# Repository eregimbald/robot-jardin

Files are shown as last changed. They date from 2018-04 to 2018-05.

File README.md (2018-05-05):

# robot-jardin

A controller to automate watering of an indoor tomato farm.

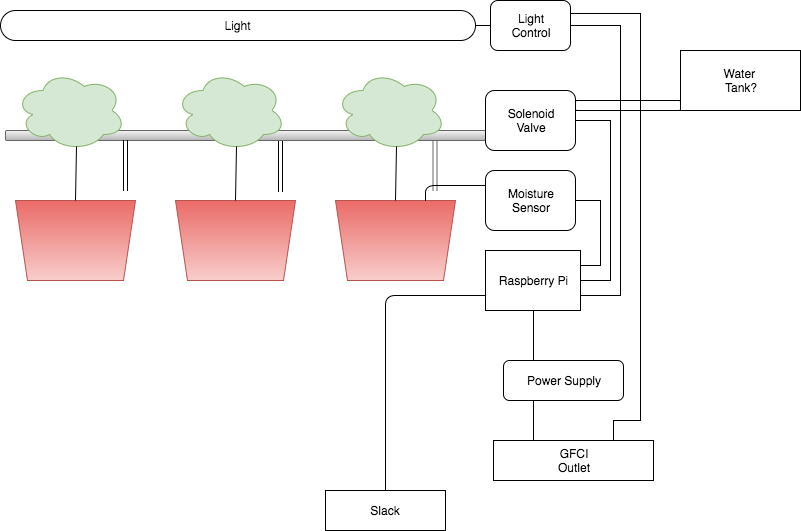
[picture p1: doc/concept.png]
Concept


* Moisture sensors for soil.
* Solenoids to control watering.
* Hoses and T pieces to direct water into the pots.
* A LED light system. Mechanism to turn on and turn off the lights.
* Slack integration to the Raspberry Pi for control and monitoring.

## Requirements

### Platforms

- Raspbian

#### Configuration

##### wifi-interface
```
sudo nano /etc/network/interfaces

auto wlan0
iface wlan0 inet static
  address 192.168.1.180
  netmast 255.255.255.0
  gateway 192.168.1.1
  wpa-conf /etc/wpa_supplicant/wpa_supplicant.conf
```

##### wpa_supplicant
```
sudo nano /etc/wpa_supplicant/wpa_supplicant.conf

country=CA
ctrl_interface=DIR=/var/run/wpa_supplicant GROUP=netdev
update_config=1

network={
    ssid="ssid"
    psk="psk"
}
```

##### Enabling services
```
sudo raspi-config
Interfacing options
Enable ssh
Enable SPI
```
## Packages

Everything runs on Python3

### spidev
```
sudo apt-get install python3-spidev
wget https://github.com/Gadgetoid/py-spidev/archive/master.zip
unzip master.zip
rm master.zip
cd py-spidev-master
sudo python setup.py install
cd ..
```
### Adafruit Python GPIO
```
sudo apt-get update
sudo apt-get install build-essential python-pip python-dev python-smbus git
git clone https://github.com/adafruit/Adafruit_Python_GPIO.git
cd Adafruit_Python_GPIO
sudo python setup.py install
sudo python3 -m pip install git+git://github.com/chrisb2/pi_ina219.git
```
### Adafruit Python MCP3008
```
sudo apt-get update
sudo apt-get install build-essential python-dev python-smbus python-pip
sudo pip3 install adafruit-mcp3008
```
## MISC
https://github.com/stefanwichmann/kelvin

https://www.amazon.ca/Irrigation-System-Sprinkler-Watering-Outdoor/dp/B073NBHRRD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

http://www.davidhunt.ie/water-droplet-photography-with-raspberry-pi/

## Hardware
* To use a piece of proto board, with a Raspberry PI expansion connector.
* Thru-hole components
* A power adapter rated at 12V, 5A (this is more than enough, but commodity available on Amazon).
* A 5V regulator circuit (So we can use the same power brick for powering the PI as well).
* moisture sensors connected to an AD converter.
* water valve solenoid controlled by transistors.
* lights controlled by switching a plug.

Where possible datasheets for the parts we have thought about using are in the doc/datasheets folder.

## Raspberry Pi
We have the Raspberry Pi 3B. We want to use this, for the familiarity of programming language (Python).

Also we wish to have slack integration for remote query, monitoring, and control of the device.

### Power adapter
We needed 12V to drive the solenoid.  The solenoid takes about 100mA of power.  Plus we need to consider the power requirements of the Raspberry Pi.

We found this on Amazon for $12
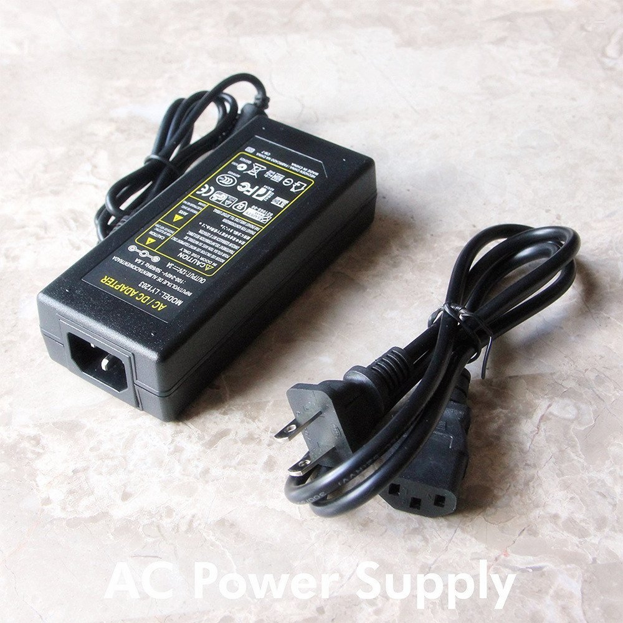
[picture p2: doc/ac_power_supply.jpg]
AC power supply


It sais it is for LED strip lighting. 12V rated at 5A.  This will be more than enough for our uses.

## Voltage Regulator
Rather than needing a 2nd power brick adapter for powering the Raspberry Pi, which is another plug in the power bar, and another cable, and that micro USB power connector that never stays plugged in nicely (compared to a barrel jack power connector), it would be better if we could power the Raspberry Pi from our power adapter.

Several sites recommend that you use the USB input, because the Pi has built in power protection for you, so that if you accidentally give it more than 5V input you won't wreck you Pi.

Here, if we use a good 5V stable voltage regulator, then we should not have any problems with our Pi. Unless we drop the Pi into a bucket of water. But really that will have more problems than electrical power input considerations.

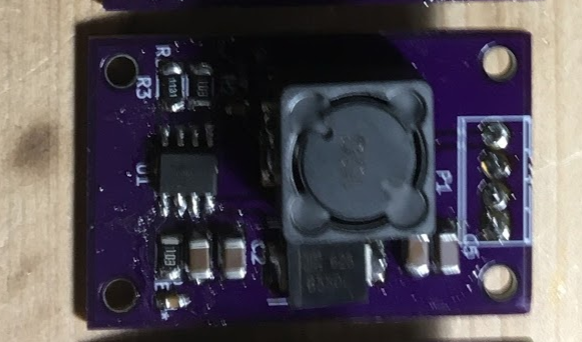
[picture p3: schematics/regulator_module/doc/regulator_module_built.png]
voltage regulator


This was from a different project where I was going to use this to drive some stepper motors. It should have enough power to handle the Pi.

### Moisture Sensor Inputs
These moisture sensors came with a small intermediate circuit board. This module has a comparator on it, so that it can produce a digial output. Our initial experiments found this to be not very reliable or accurate, or consistent. Turning that little potentiometer is hard to get it to where we want. And also, what does it mean. It does not leave room for adjustments in software. The board also has an analog output. But really this is just using a resistor to create a voltage divider type of circuit across the probe input. We have chosen to use this analog mode of the sensor.  So instead of needing to use this little circuit board it would be better if we just built the components onto our own circuit board. This way we can have just a pair of wires from the circuit board to the moisture sensor.

We analyzed the circuit board and it contains these components.

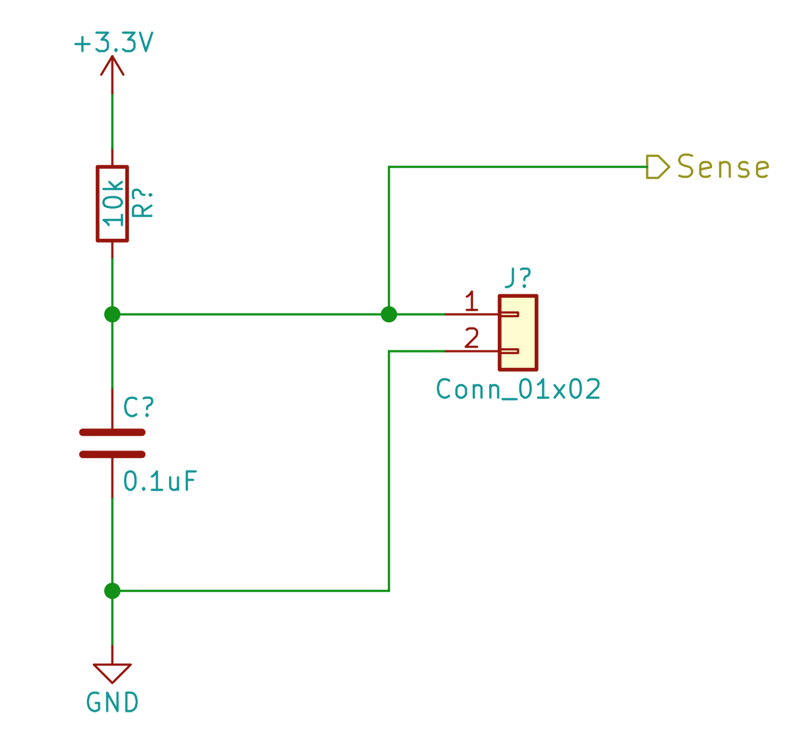
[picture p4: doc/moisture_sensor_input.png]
Moisture Sensor Input


Where the connector can be one of those screw terminal PCB mount connectors.  The wires we can use to go to the probe can be one of the pairs from a regular cat5 network cable type twisted pair wire, and then as long as we need to reach the potted plants from where the sensor is installed.

The sense goes straight into our analog to digital converter (currently the MCP3008 device).

When the soil is dry, the output will be a higher voltage. As the soil gets more moist, the probes will have a lower resistance, and thus create a lower voltage to the ADC.

Here we have chosen to use 3.3V as analog the input to the probes, since this is what the IO pins to the Raspberry Pi will use. The MCP3008 Supports separate Analog reference, but only as long as this is less than or equal to the VDD input.  Using 5V might possibly give us a better details when considering the small resistance that will be added from length of the wires to the probes. And 5V also lets us use faster samples. But really we are only going to be reading a few times a minute (or otherwise very low sample rate here).

#### One thing to note: Minimun dryness Threshold in software.

We should calibrate our software to expect the soil has a minimum dryness.  In that if the soil is below this threshold value then we do not attempt to try to water the soil. (e.g. we have a reading less than the maximum voltage possible).

This is because we have no way to differentiate between really dry soil, and if the probes are entirely not connected at all. such as there is no wires hooked up to the Raspberry Pi.  or in a more likely real world use case, if the wires on the probe corroded or the probe corroded or is no longer working.

In this situation (probes disconnected), when the soil appears dry to us, if we turn on the solenoid to let water in, the soil will never actually give a reading of "not dry" (because the probes are broken or disconnected). And we end up flooding the plants, and possibly making a mess of the apartment.

The proposal here then is to require the soil be some what moist. (e.g. so we are able to read a slightly lower voltage than just the max voltage). And then work with adjusting the soil moisture to be more moist within this. Assuming of course that we are able to read a minimum moisture that is within the range of what we would want the plants to be.

### Analog to digital controller
As discussed earlier, it is preferred we read the moisture sensor analog output, instead of its digital output, as our testing found there is not a very meaningful output from the moisture sensor digital output. Other than it is amusing for a test circuit on a breadboard.

The Raspberry Pi has no analog inputs. So we need something that can provide us with analog to digital conversion. For this we have selected the MCP3008 device.
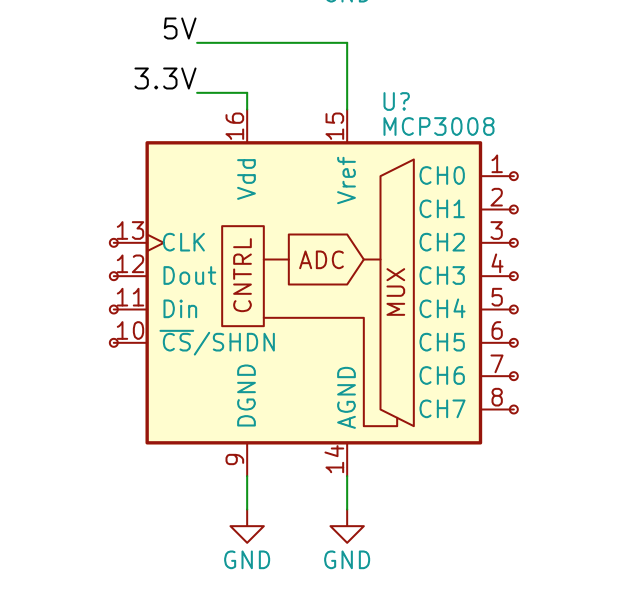
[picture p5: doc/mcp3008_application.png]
MCP3008 application


This is because this is a popular and inexpensive device, that is available in a 16-dip package, and has a good community supported driver.

It also has 8 channels. So we can readily connect up to 8 analog inputs. Such as moisture sensors, or anything that can provide us a voltage , like ambient light sensors, noise sensors, pressure sensors, potentiometers, etc.

Our immediate use will be a few moisture sensors.

### Solenoid Driver
We can use a basic digital IO pin from the Raspberry Pi to drive a solenoid.  The solenoid we have choosen works around 12V and uses about 100mA of current. A simple transistor driver circuit is good enough for this.

But we thought there should be some short circuit protection, in case we short out the wires to the solenoid, or the solenoid becomes connected to ground. This circuit below attempts to provide this protection.

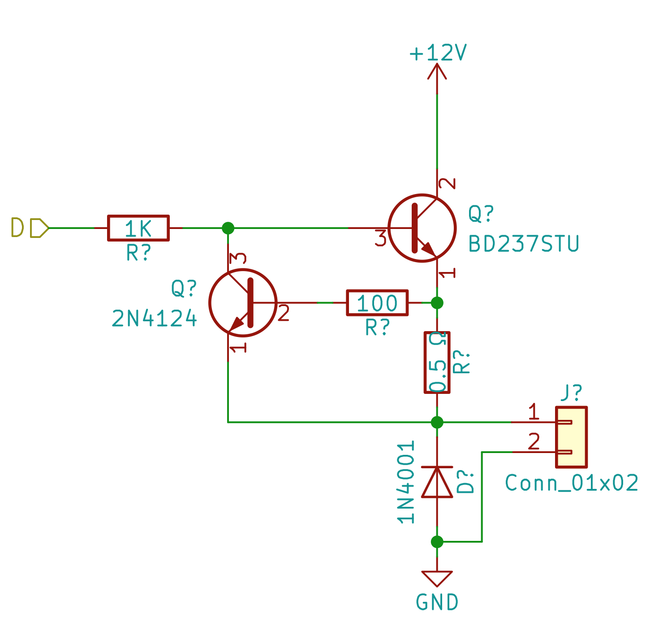
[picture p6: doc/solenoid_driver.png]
solenoid driver


The input from the Raspberry Pi digital IO pin of logic level HIGH will turn on the solenoid.  I prefer this option from the usual Ali express type of relay board. Where they have the opto isolators and relays, which can be used for anything from 12 VDC to 120 VAC. But they are active low inputs. Which means when you power on the Pi and the GPIO pins are logic level LOW by default, this will turn on the relays until our software boots up and asserts logic level HIGH to the pin.

Practically these relay boards do this to allow for more general compatibility with microcontrollers. Most semiconductor devices are able to sink more current (pull a pin low) then they are able to source current (pull a pin high). Here this is a mute point since we are using a transitor driver which uses much less current than the opto isolators (about 20 mA) on a relay board.

The 12V power for the solenoid will be provided by the power supply brick above.

### Plug Driver
To control the lighting for the plants we assume something that can handle being powered on and off by unplugging it. Such as a lamp with a switch that can be turned on and have the lamp come on when it is plugged in.

We have thought about using relays, but really it is more elegant to use Triac device with an opto isolator. This is the same feature and behavior as a solid state relay, only not as expensive. Here we are assuming we ae not using heavily inductive loads and thus do not require power conditioning or snubbering (beyond what the Trac provides).

Using these STMicroelectronics Snubberless series Triacs.
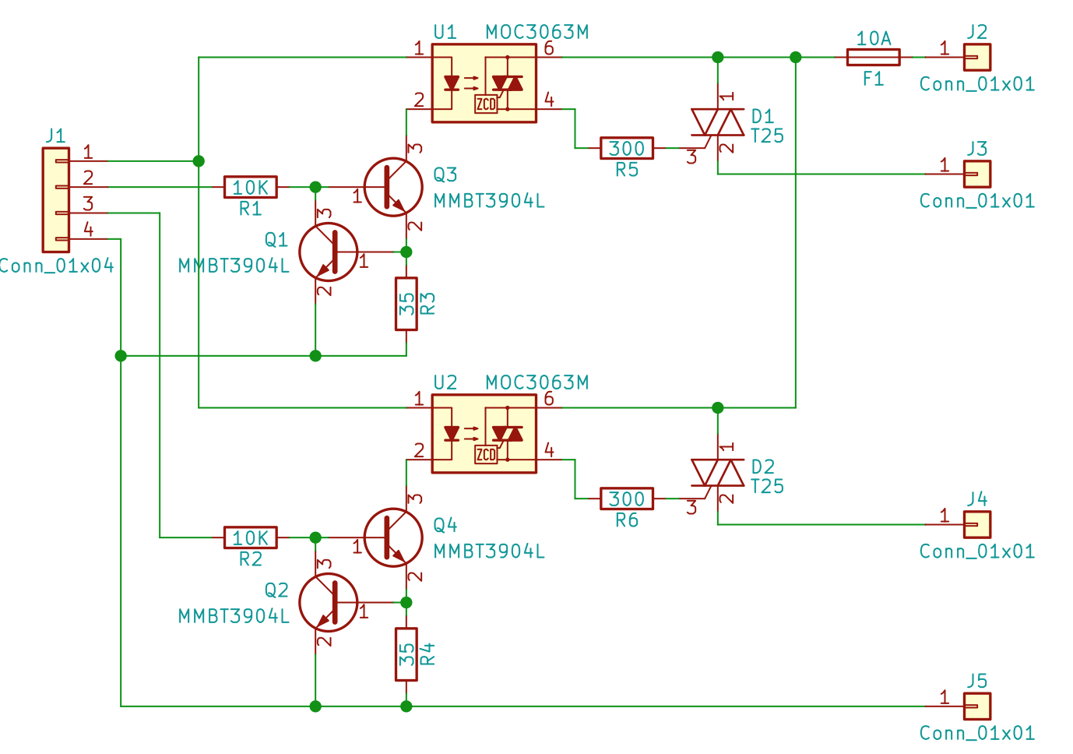
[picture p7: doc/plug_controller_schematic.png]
plug controller schematic


We have a connector there for AC ground to be also our ground.

This is actually two swiches. The idea being that in a standard duplex plug there are two halves (top and bottom). So that we can provide individual switching to each half. Which will allow us to plug two lights into a single duplex plug.

The board can be laid out small enough to fit inside a metal duplex outlet style box. So that we can provide control wires into the box.
I was invisioning an extension cord with the metal plug box on the end with this controller board inside the metal box.

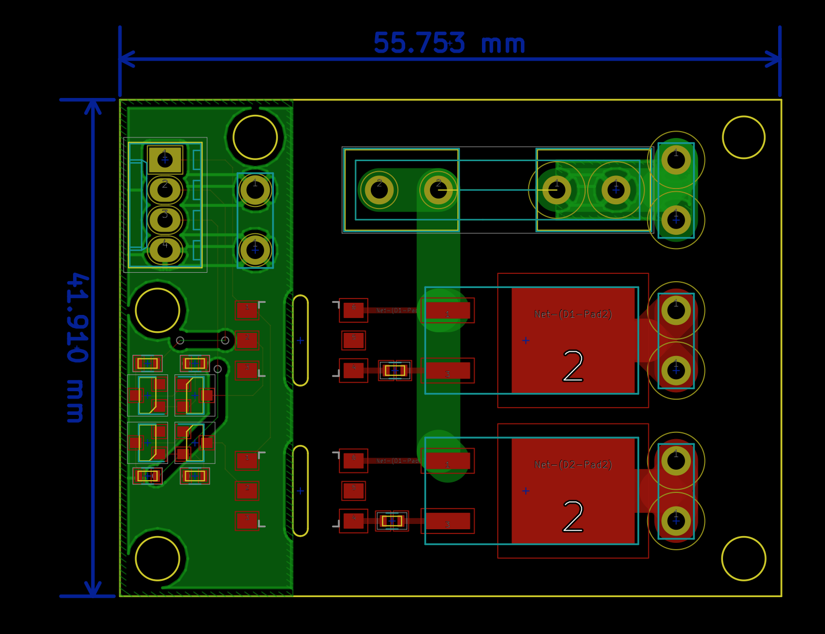
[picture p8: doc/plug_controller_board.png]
plug controller board

This keeps all of the 120V AC inside the extension cord and outlet box. We do not need to have 120V wires going out of the box to our circuit board. Which is a good thing here, since we are working with both water and electricity.

So to use this we will just need 2 digital IO pins from the Pi.

## IO expander

If we will have a lot of digital IO pins, such as to drive the solenoids and plug drivers, then it is recommended we look into a port expander.

A device such as the MPC32017 will do this well
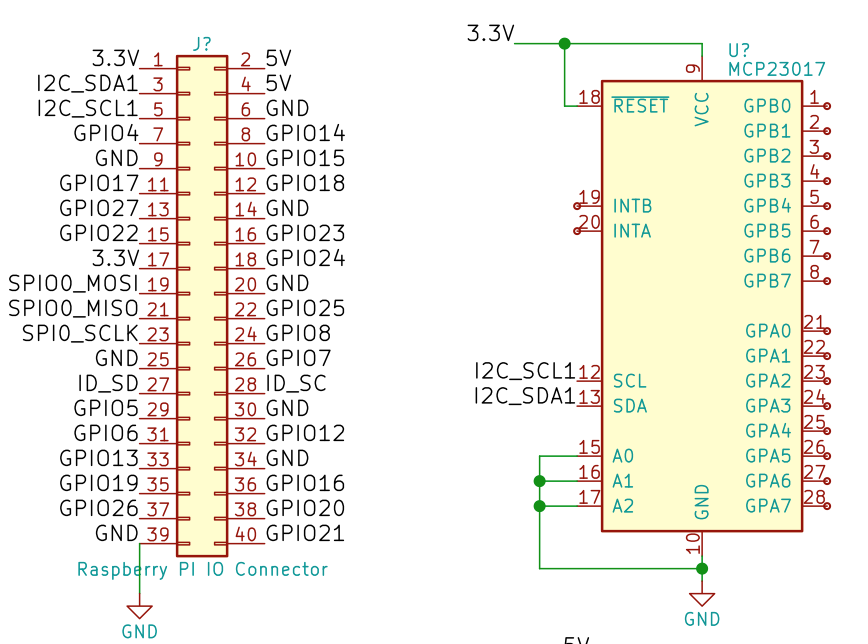
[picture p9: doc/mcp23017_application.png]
MCP23017 application


here it requires (2) GPIO pins from the Raspberry Pi (the I2C bus pins) and provides us 16 pins, which can individually be configured as inputs or outputs.

If we were using them as digital inputs, then we would need some another GPIO pins for connecting those INTA, INTB pins. Which are for notifying the Raspberry Pi there is a pin state change on an input pin.

## Other Considerations

The site where this is installed should have a ground fault circuit interrupt (GFCI) type outlet installed into the wall.

This is where we will plug in
* The power adapter for powering the Raspberry Pi and solenoids and controlling the lights.
* The controlled plug for the lighting for the plants.

This is because we are working with water here.  According to Canadian buliding code, electrical applicances used near water, such as in a bathroom or kitchen, should be serviced from a GFCI outlet.

It is also beyond the scope of this project to instruct how to obtain and install a GFCI outlet. Consult your local electrician or home improvement store.

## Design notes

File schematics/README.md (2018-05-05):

# Schematics
These are KiCAD projects.

KiCAD is an  cross platform and open source Electronics Design Automation Suite.

We used it here for making schematic diagrams and where we had a PCB made, the PCB layout.

You can get it here: [KiCAD Project](http://kicad-pcb.org/)

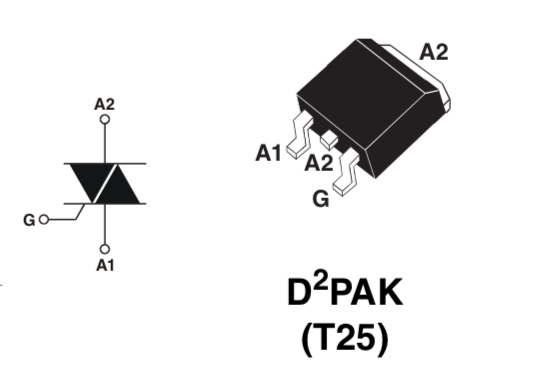
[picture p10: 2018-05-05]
doc/datasheets/D25_pinout.png

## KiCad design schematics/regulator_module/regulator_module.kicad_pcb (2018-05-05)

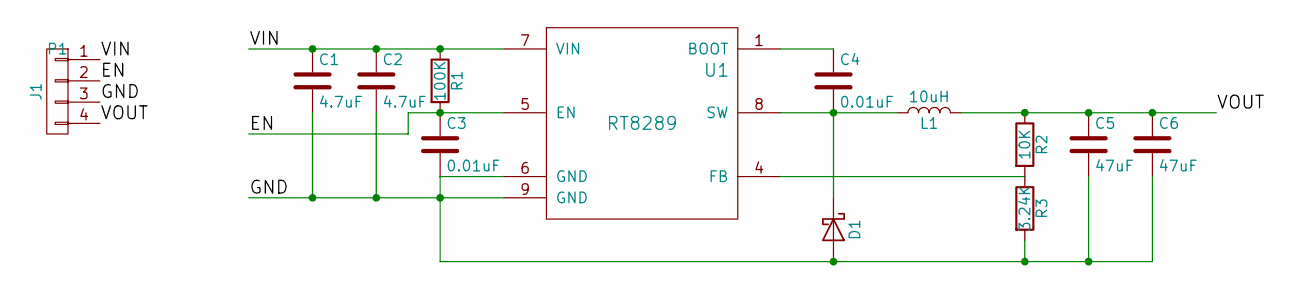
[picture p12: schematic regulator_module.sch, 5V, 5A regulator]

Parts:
C1, C2: 4.7uF; C_1206
C3, C4: 0.01uF; C_0603
C5, C6: 47uF; C_1206
D1: B550C-13-F; DO-214AB
L1: 10uH; Inductor_SMD_12.7mm
P1: J1; TerminalBlock_Pheonix_MPT-2.54mm_4pol
R1: 100K; R_1206
R2: 10K; R_1206
R3: 3.24K; R_1206
U1: RT8289; SOP-8_Exposed_Pad

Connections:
/EN: C3.1, P1.2, R1.2, U1.5 (EN)
/GND: C1.2, C2.2, C3.2, C5.2, C6.2, D1.2 (A), P1.3, R3.2, U1.6 (GND), U1.9 (GND)
/VIN: C1.1, C2.1, P1.1, R1.1, U1.7 (VIN)
/VOUT: C5.1, C6.1, L1.2, P1.4, R2.1
unnamed: C4.1, U1.1 (BOOT)
unnamed: C4.2, D1.1 (K), L1.1, U1.8 (SW)
unnamed: R2.2, R3.1, U1.4 (FB)

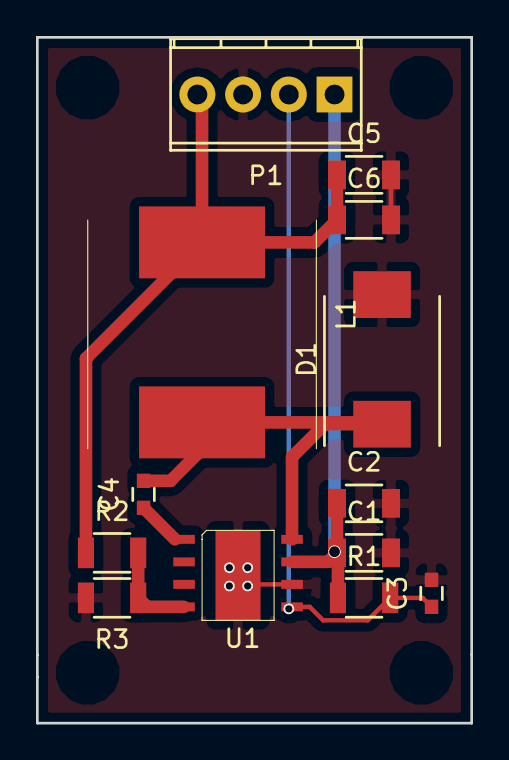
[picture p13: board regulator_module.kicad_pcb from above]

Board: 2 copper layers, 24.1 x 38.1 mm, 13 parts (0 on the bottom side), 7 nets.

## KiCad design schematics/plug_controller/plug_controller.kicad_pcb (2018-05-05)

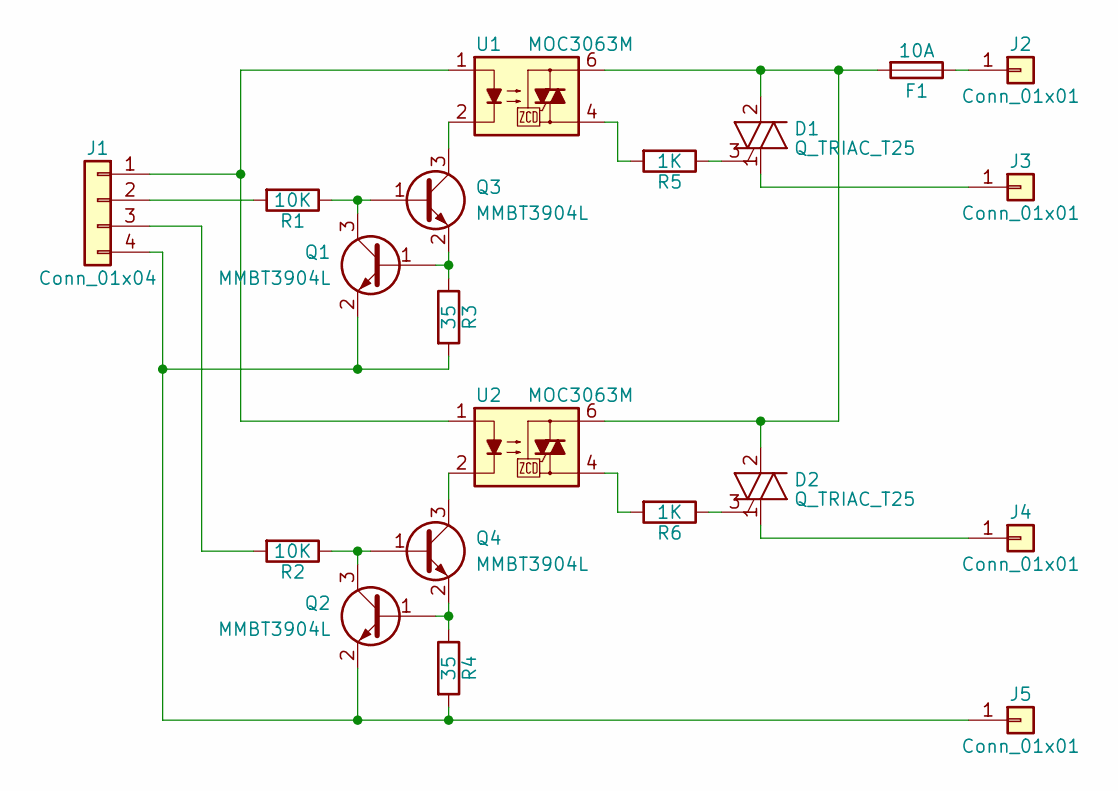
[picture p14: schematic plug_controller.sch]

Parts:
D1, D2: Q_TRIAC_T25; D2PAK
F1: 10A; Fuseholder5x20_horiz_open_lateral_Type-II
J1: Conn_01x04; Molex_KK-6410-04_04x2.54mm_Straight
J2, J3, J4, J5: Conn_01x01; TAB_0.250_SOLDER
Q1, Q2, Q3, Q4: MMBT3904L; SOT-23
R1, R2: 10K; R_0603
R3, R4: 35; R_0603
R5, R6: 1K; R_0603
U1, U2: MOC3063M; 6-SMD_Gullwing

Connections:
unnamed: D1.1 (A2), J3.1
unnamed: D1.2 (A1), D2.2 (A1), F1.2, U1.6, U2.6
unnamed: D1.3 (G), R5.1
unnamed: D2.1 (A2), J4.1
unnamed: D2.3 (G), R6.1
unnamed: F1.1, J2.1
unnamed: J1.1, U1.1, U2.1
unnamed: J1.2, R1.2
unnamed: J1.3, R2.2
unnamed: J1.4, J5.1, Q1.2 (E), Q2.2 (E), R3.2, R4.2
unnamed: Q1.1 (B), Q3.2 (E), R3.1
unnamed: Q1.3 (C), Q3.1 (B), R1.1
unnamed: Q2.1 (B), Q4.2 (E), R4.1
unnamed: Q2.3 (C), Q4.1 (B), R2.1
unnamed: Q3.3 (C), U1.2
unnamed: Q4.3 (C), U2.2
unnamed: R5.2, U1.4
unnamed: R6.2, U2.4

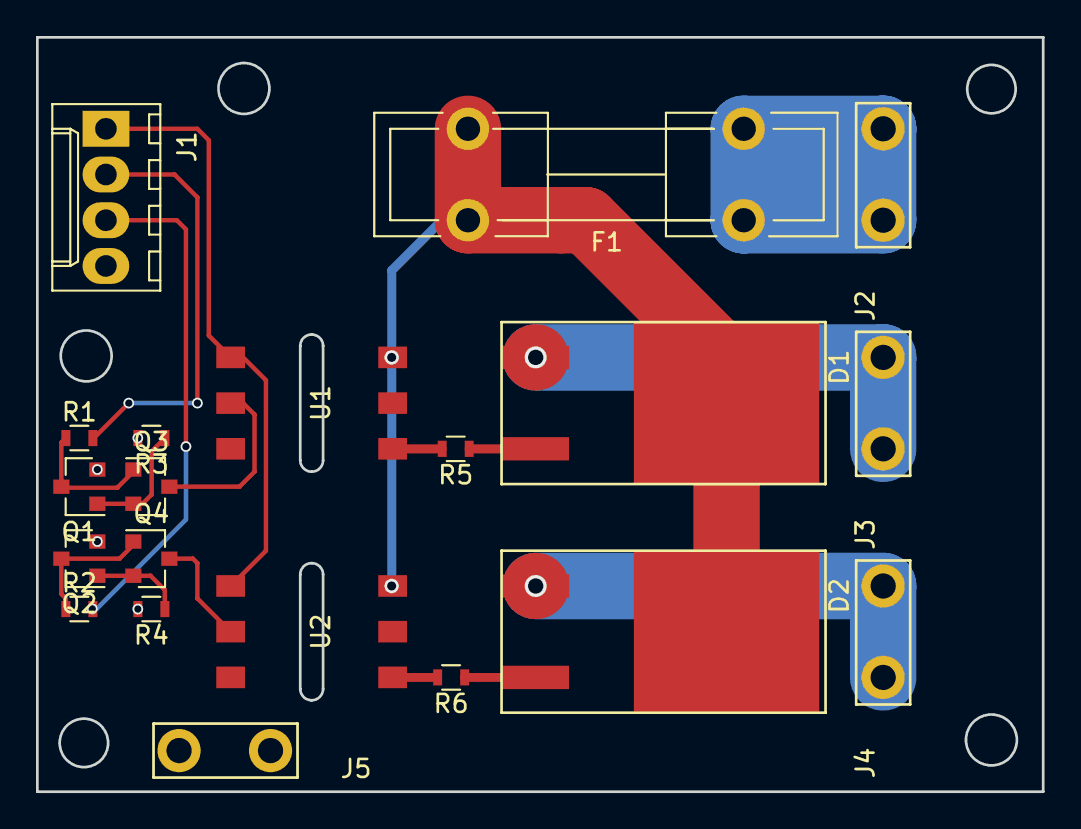
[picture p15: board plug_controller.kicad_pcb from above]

Board: 2 copper layers, 55.9 x 41.9 mm, 20 parts (0 on the bottom side), 18 nets.

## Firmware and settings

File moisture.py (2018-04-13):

#!/usr/bin/python3.5

# Basic imports
import time
import statistics

# Import SPI library (for hardware SPI) and MCP3008 library.
import Adafruit_GPIO.SPI as SPI
import Adafruit_MCP3008

# Hardware SPI configuration:
SPI_PORT   = 0
SPI_DEVICE = 0
mcp = Adafruit_MCP3008.MCP3008(spi=SPI.SpiDev(SPI_PORT, SPI_DEVICE))

# Setting up looping parameters
loops = 10
channels = 8
readings = {}

# Reading sensor values and storing them in an array
for loop in range(loops):
    print(loop)
    readings[loop] = {}
    for read in range(channels):
        readings[loop][read] = mcp.read_adc(read)
    time.sleep(0.5)

for k, v in readings.items():
    print(k,v)

for chan in range(channels):
    #for k, v in readings.items():
    #    print(v[chan])
    print("\nChannel: {}".format(chan))
    print(statistics.mean(v[chan] for k, v in readings.items()))

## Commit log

2018-04-15 do some design documentation.
    some schematics
    finding datasheets for the components we were thinking about using
    pictures of the schematics in the README.
    [analog_input.kicad_pcb, analog_input.sch, moisture_sensor.sch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]
2018-04-29 update footprints as assembling first design.
    The triac pins were reversed.
    The fuse footprints were not the holders i have.
    The resistor between optotriac and triac should be larger.
    [plug_controller.kicad_pcb, plug_controller.sch]
